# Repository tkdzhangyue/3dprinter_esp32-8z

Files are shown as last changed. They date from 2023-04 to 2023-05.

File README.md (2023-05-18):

# 3Dprinter_esp32-8z_tmc2226
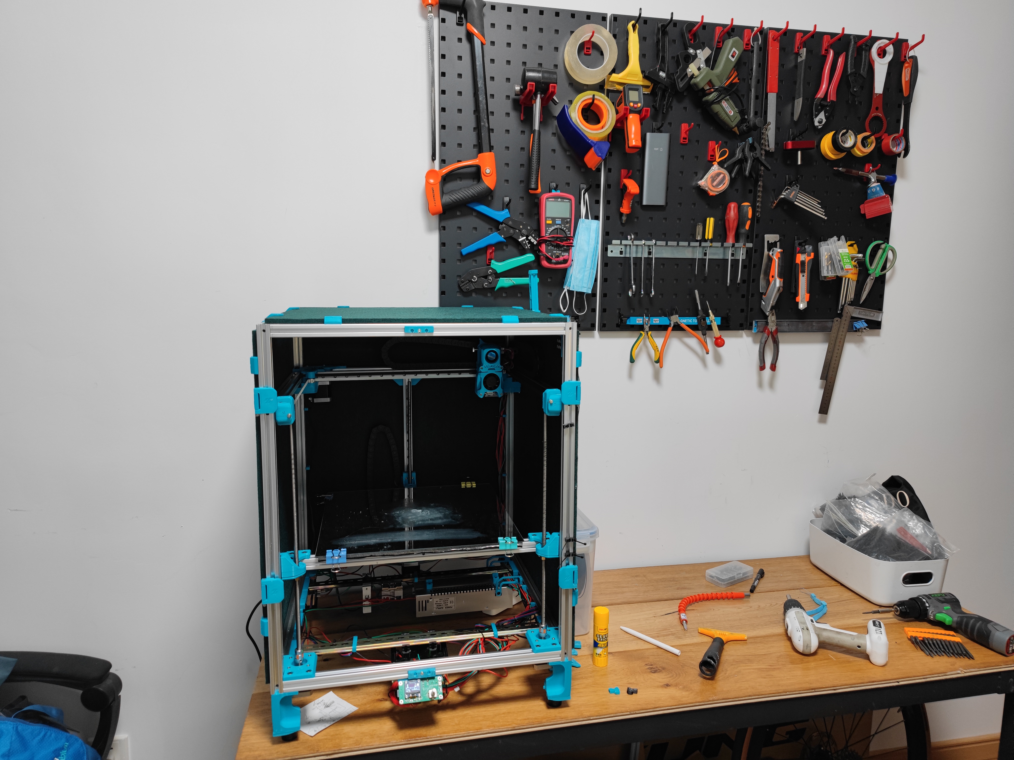
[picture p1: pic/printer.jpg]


## B站视频:
    1. 待更新
    2. 待

## 开源打印机过程中,遇到并且趟平的大坑们.
    1. 待总结.

## ESP32作3D打印机主控的优点
    1. 有wifi，升级固件很方便。
    2. 通过浏览器上传打印Gcode文件。
    3. 修改config参数，也可以在浏览器上进行。
## 缺点
    1. ESP32的引脚少， 不能接丰富的传感器。打印机腔室温度，用常开温度开关接风扇实现。
    2. 不能通过浏览器监控打印进度， 只能启动打印。
## Marlin固件
    根据B站祁同学的2.0.9版本，作了一份提交到2.1.2版本.
    主要修改: 
    1. 步进电机驱动修改为板载一体焊接的TMC2226，优点是比tmc2209好焊接，设置所有参数相同。
    2. 开了X/Y/E0的TMC驱动的UART模式, 速度超过100转换高速模式.注：需要在板上连接对应跳线。
    3. 1号风扇切片软件控制，2号风扇在打印头超过100℃时开启.
    4. 开了热床自动对齐(Z_STEPPER_AUTO_ALIGN),Trident的三点式:
        #define Z_STEPPER_ALIGN_XY { {270, 270 }, {80,  270}, { 175, 80 } }
        注：本机350*350*350尺寸。
    4. 开了热床自动调平(AUTO_BED_LEVELING_BILINEAR)
    5. 屏幕使用TINY_BOY小屏幕，2根线很节约ESP32的引脚资源。
    6. Marlin版本升级到2.1.2之后, 不会遇到2.0.9的bug,比如wifi和oled需要重新编译2次的问题.

## 硬件
    为了防止完全小白的朋友贸然掉入开源打印机的大坑里, 有好多半路翻车的voron2.4/Trident. 目前打算只上传电路图/去掉连线的PCB图. 
    所以, 需要一定的电路/PCB布线的知识储备,贴片焊接的技术手法.
    注: 如果嘉立创表示被大家白嫖完全不介意的话, 也有可能上传完全版图.
### VORON Trident
1. 打印机尺寸350*350*350，进程挤出机。
2. 热床： 
* 加热，碳纤维加热丝，DIY
* 打印平台，下边用弹簧支撑，大概1mm的弹性行程；上边0.5mm白铁板+1mm的普通镜子。
3. 打印头：
* V6散热+特氟龙M6喉管+火山加热块+0.6mm打印嘴。
* Q5MC2需要下移一些，量一下大概位置，用m3注塑螺母烫一下。
* 打印一些大尺寸的工程零件，比如dummy的零件，可以换成0.8mm的喷嘴。
4. 打印速度：目前1500加速度，150mm/s速度, 300mm/s空驶速度.
5. TMC2226电流:E0=1000mA, XY=1500mA.
6. 主板散热风扇常开, XY轴散热片垒3层. 腔室散热用65℃常开开关控制风扇.

## 附加打印件
    1. 主板散热风扇支架
    2. 腔室温控排风，接80螺纹管。
    3. 用8mm聚酯纤维板封箱的,2020管材扣件.

## Cura打印机设置
打印机尺寸是350*350*350,根据实际情况酌情修改.

开始G-code
```
G92 E0 ; Reset Extruder
G28 ; Home all axes
G34；bed align

M104 S{material_print_temperature_layer_0}
M190 S{material_bed_temperature_layer_0}
M109 S{material_print_temperature_layer_0}

G1 X320 Y320 Z0.3 F5000.0 ; Move to start position
G1 X220 Y320.0 Z0.3 F1500.0 E30 ; Draw the first line
G1 X220 Y316 Z0.3 F1500;
G1 X320 Y316 Z0.3 F1500.0 E60 ; Draw the second line
G92 E0 ; Reset Extruder
G1 Z4.0 F3000 ; Move Z Axis up little to prevent scratching of Heat Bed
G1 X175 Y175 Z0.3 F5000.0 ; Move over to prevent blob squish
```
结束G-code
```
G91 ;Relative positioning
G1 E-2 F2700 ;Retract a bit
G1 E-2 Z0.2 F2400 ;Retract and raise Z
G1 X5 Y5 F3000 ;Wipe out
G1 Z2 ;Raise Z more
G90 ;Absolute positioning

G1 X0 Y0 Z200 ;Present print
M106 S0 ;Turn-off fan
M104 S0 ;Turn-off hotend
M140 S0 ;Turn-off bed

M84 X Y E ;Disable all steppers but Z
```

``` git
commit 3e7ee928a060ad115e0529e708566712840bda35
Author: tkdzhangyue <tkdzhangyue@163.com>
Date:   Fri Apr 21 08:58:46 2023 +0800

    [esp32-8z_conf]

````

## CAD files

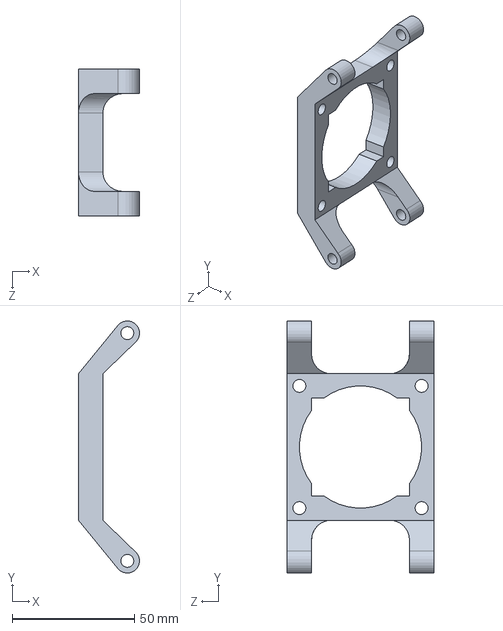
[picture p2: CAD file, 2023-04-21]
stl/mainboard_frame_ver2.SLDPRT
25.0 x 103.1 x 60.0 mm

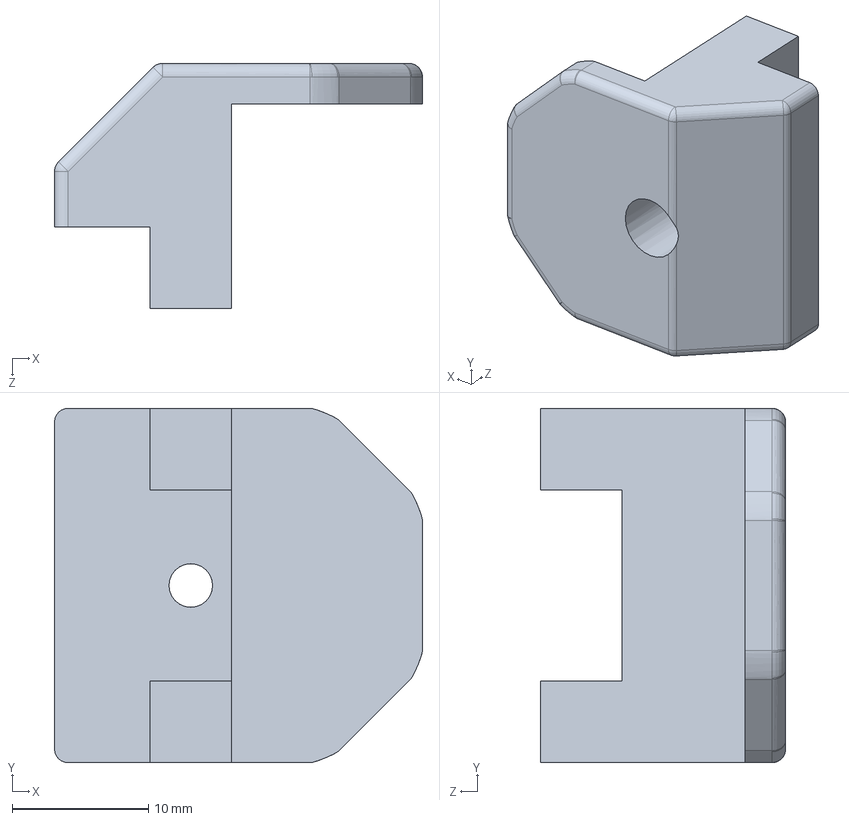
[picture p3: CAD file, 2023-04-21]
stl/trident_panel_封板支架.SLDPRT
27.0 x 26.0 x 18.0 mm

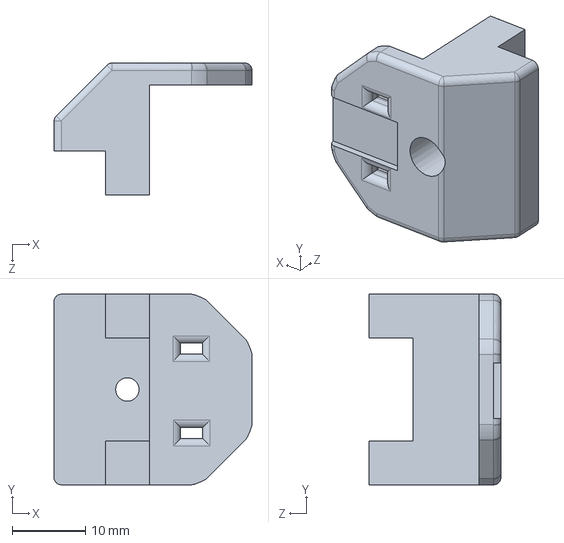
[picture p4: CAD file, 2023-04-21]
stl/charmbertemp_frame.SLDPRT
27.0 x 26.0 x 18.0 mm

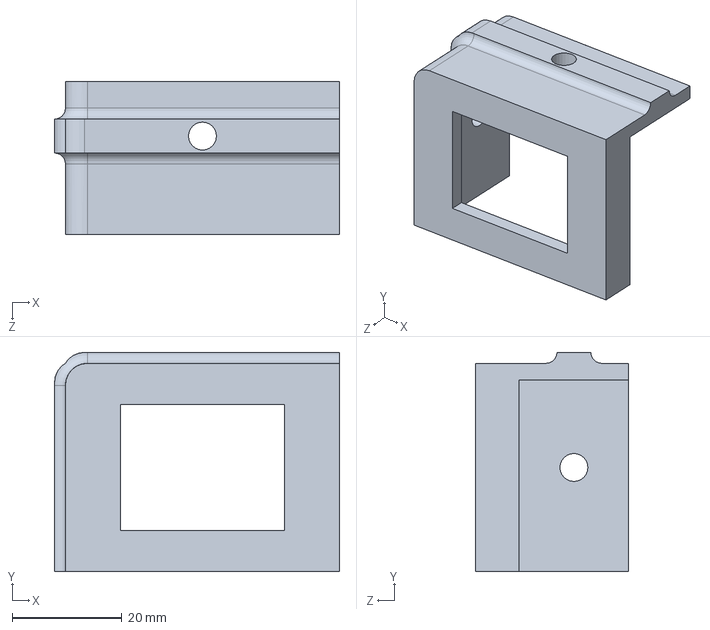
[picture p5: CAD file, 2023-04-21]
stl/light_switch.SLDPRT
52.0 x 40.0 x 28.0 mm

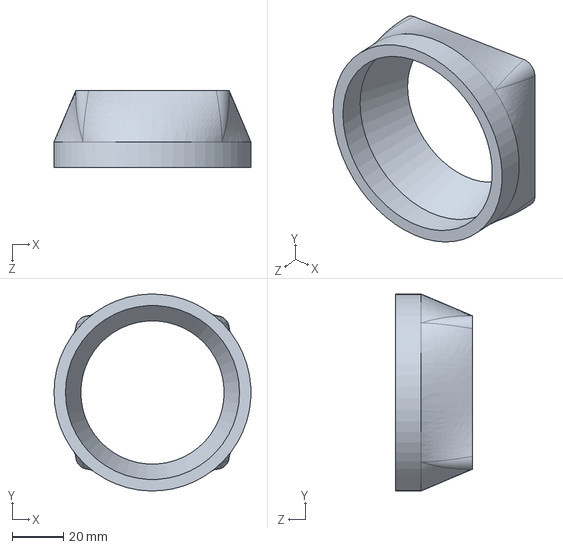
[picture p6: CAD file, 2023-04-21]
stl/exhaust_80_adapter.SLDPRT
77.0 x 77.0 x 30.0 mm

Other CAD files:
stl/charmbertemp_frame.STL
stl/exhaust_80_adapter.STL
stl/light_switch.STL
stl/mainboard_frame_ver2.STL
stl/trident_panel_封板支架.STL
